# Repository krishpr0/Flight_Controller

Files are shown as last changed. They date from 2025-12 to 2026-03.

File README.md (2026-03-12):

<h1>Flight Controller</h1>

<h5>Flight Controllers developed for Aerial Vehicles</h5>

## Components 
- **STM32F722RET6 MCU**
- **ICM-45686 IMU**
- **BMP580 BARO**
- **QMC5883P MAG**
- **MAX-M10S GPS**
- **3.3V/5V Buck Converters**
- **Micro SD Card Holder**
- **4S LiPO/LiIon**
- **4 Servo/ESCs Pins**

## PCB & Schmeatic Design 
<br>

### Schematic
Screenshot from 2026-02-10 11-39-34

<br>

### PCB


<br>

### 3D Look of the PCB
Screenshot from 2026-02-10 11-39-44

### Operation of the Product
- **Firmware** The firmware used for my current setup is the PX4, Which is know for its autonomus reliablity and efficiency.
- You can use BetaFlight, Inav, CleanFlight, Etc... and even a custom firmware!!

- This Flight Controller was made to be able to communicate with Mission Planner, PX4, etc.
- This is one of my finest creation. All of the Pervious versions were either in a Matrix board, or breadboard.

#### Reasons for making it,
- **Reason**, Firstly the reasons I started into Flight Controllers were because of Drones, I always wanted to know how it worked, how it operated, how it functions, and after looking at articles after articles, I got to know Flight Controller was the most important part for a drone to function. So i started looking at Flight Controllers, Many ppl bought pre-made Flight Controllers such as SpeedyBee, Pixhawk, etc. But those lacked features, altho the features they have are the best of the best, their circuits, But i wanted to have as much features as possible, and as well as work my way up the Flight Controllers, This Flight Controllers will be my first ever PCB made with this much functionality.

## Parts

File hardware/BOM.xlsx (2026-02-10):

No. | Quantity | Comment | Designator | Footprint | Value | Manufacturer Part | Manufacturer | Supplier Part | Supplier
1 | 4 | Test-Point | +5V,GND,U3_RX,U3_TX | Test-Point-0.5mm
2 | 2 | TS-1088-AR02016 | BOOT1,RESET1 | SW-SMD_L3.9-W3.0-P4.45 |  | TS-1088-AR02016 | XUNPU(讯普) | C720477 | LCSC
3 | 5 | Device_C | C7,C8,C9,C12,C31 | C0603 | 10uF
4 | 5 | Device_C | C10,C11,C13,C17,C18 | C0603 | 22uF
5 | 13 | Device_C | C14,C15,C19,C20,C21,C22,C23,C24,C25,C26,C27,C37,C38 | C0603 | 100nF
6 | 2 | Device_C | C16,C32 | C0603 | 2.2uF
7 | 3 | Device_C | C28,C29,C30 | C0603 | 1uF
8 | 2 | Device_C | C33,C34 | C0603 | 20pF
9 | 2 | Device_C | C35,C36 | C0603 | 6.8pF
10 | 1 | Device_C | C40 | C0603 | 4.7uF
11 | 1 | Device_C | C41 | C0603 | 0.1uF
12 | 1 | TF-01A | Card1 | TF-SMD_TF-01A |  | TF-01A | 韩国韩荣 | C91145 | LCSC
13 | 1 | HX PH254-01-04-Z-L11.5 straight pin header | H1 | HDR-TH_4P-HX-PH254-01-04-Z-L11.5 |  | HX PH254-01-04-Z-L11.5 straight pin header | hanxia(韩下) | C52016392 | LCSC
14 | 2 | 1.5uH | L1,L6 | IND-SMD_L4.0-W4.0-A | 1.5uH | XFL4020-152MEC | Coilcraft(线艺) | C3033018 | LCSC
15 | 1 | FCM1608KF-601T03 | L4 | L0603 |  | FCM1608KF-601T03 | TAI-TECH(台庆) | C141723 | LCSC
16 | 1 | 5.6uH | L7 | IND-SMD_L3.0-W3.0 | 5.6uH | YHNR3015-5R6M | YJYCOIN(益嘉源) | C18236327 | LCSC
17 | 1 | LED_0402-R | LED1 | LED0402-RD_YELLOW
18 | 4 | HX PH254-01-03-Z-L11.5 pcb pin header | M1,M2,M3,M4 | HDR-TH_3P-P2.54-V-M-1 |  | HX PH254-01-03-Z-L11.5 pcb pin header | hanxia(韩下) | C52016391 | LCSC
19 | 1 | PDTC114EU,115 | Q1 | SOT-323-3_L2.0-W1.3-P1.30-LS2.1-BR |  | PDTC114EU,115 | Nexperia(安世) | C135830 | LCSC
20 | 2 | Device_R | R1,R2 | C0201 | 5.1K
21 | 9 | Device_R | R12,R13,R16,R17,R18,R19,R20,R21,R22 | C0201 | 10K
22 | 1 | Device_R | R14 | C0201 | 100K
23 | 1 | Device_R | R15 | C0201 | 22.1K
24 | 1 | Device_R | R23 | C0201 | 820
25 | 1 | Device_R | R24 | C0201 | 10
26 | 2 | Device_R | R25,R26 | C0201 | 4.7k
27 | 1 | 6GHz | RF1 | RF-SMD_U.FL-R-SMT-1-80 | 6GHz | U.FL-R-SMT-1(01) | HRS(广濑) | C598199 | LCSC
28 | 1 | ICM-45686 | U2 | LGA-14_L3.0-W2.5-P0.50-TL |  | ICM-45686 | TDK InvenSense(应美盛) | C22459454 | LCSC
29 | 1 | STM32F722RET6 | U3 | LQFP-64_L10.0-W10.0-P0.50-LS12.0-BL |  | STM32F722RET6 | ST(意法半导体) | C118207 | LCSC
30 | 1 | TPS63070RNMR | U5 | VQFN-HR-15_L3.0-W2.5-P0.50-BL_TPS63070RNMR |  | TPS63070RNMR | TI(德州仪器) | C109322 | LCSC
31 | 1 | LMR51430XDDCR | U6 | SOT-23-6_L2.9-W1.6-P0.95-LS2.8-BL |  | LMR51430XDDCR | TI(德州仪器) | C5185863 | LCSC
32 | 1 | MAX-M10S-00B | U7 | SMD-18_L10.1-W9.7-P1.10-TL_SKG09F |  | MAX-M10S-00B | U-BLOX | C4153167 | LCSC
33 | 1 | QMC5883P | U8 | LGA-16_L3.0-W3.0-P0.50-BL_SQ |  | QMC5883P | QST(上海矽睿) | C2847467 | LCSC
34 | 1 | BMP580 | U9 | LGA-10_L2.0-W2.0-P0.50-TL_BMP580 |  | BMP580 | Bosch(博世) | C22391138 | LCSC
35 | 1 | TYPE-C 16PIN 2MD(073) | USB1 | USB-C-SMD_TYPE-C-6PIN-2MD-073 |  | TYPE-C 16PIN 2MD(073) | SHOU HAN(首韩) | C2765186 | LCSC
36 | 1 | 25MHz | X1 | CRYSTAL-SMD_4P-L3.2-W2.5-BL | 25MHz | X322525MOB4SI | YXC(扬兴晶振) | C9006 | LCSC
37 | 1 | 32.768kHz | X2 | OSC-SMD_2P-L3.2-W1.5 | 32.768kHz | ABS07-32.768KHZ-T | ABRACON | C130253 | LCSC

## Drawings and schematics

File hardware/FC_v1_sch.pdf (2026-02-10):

# Pressure Sensor

# IMU

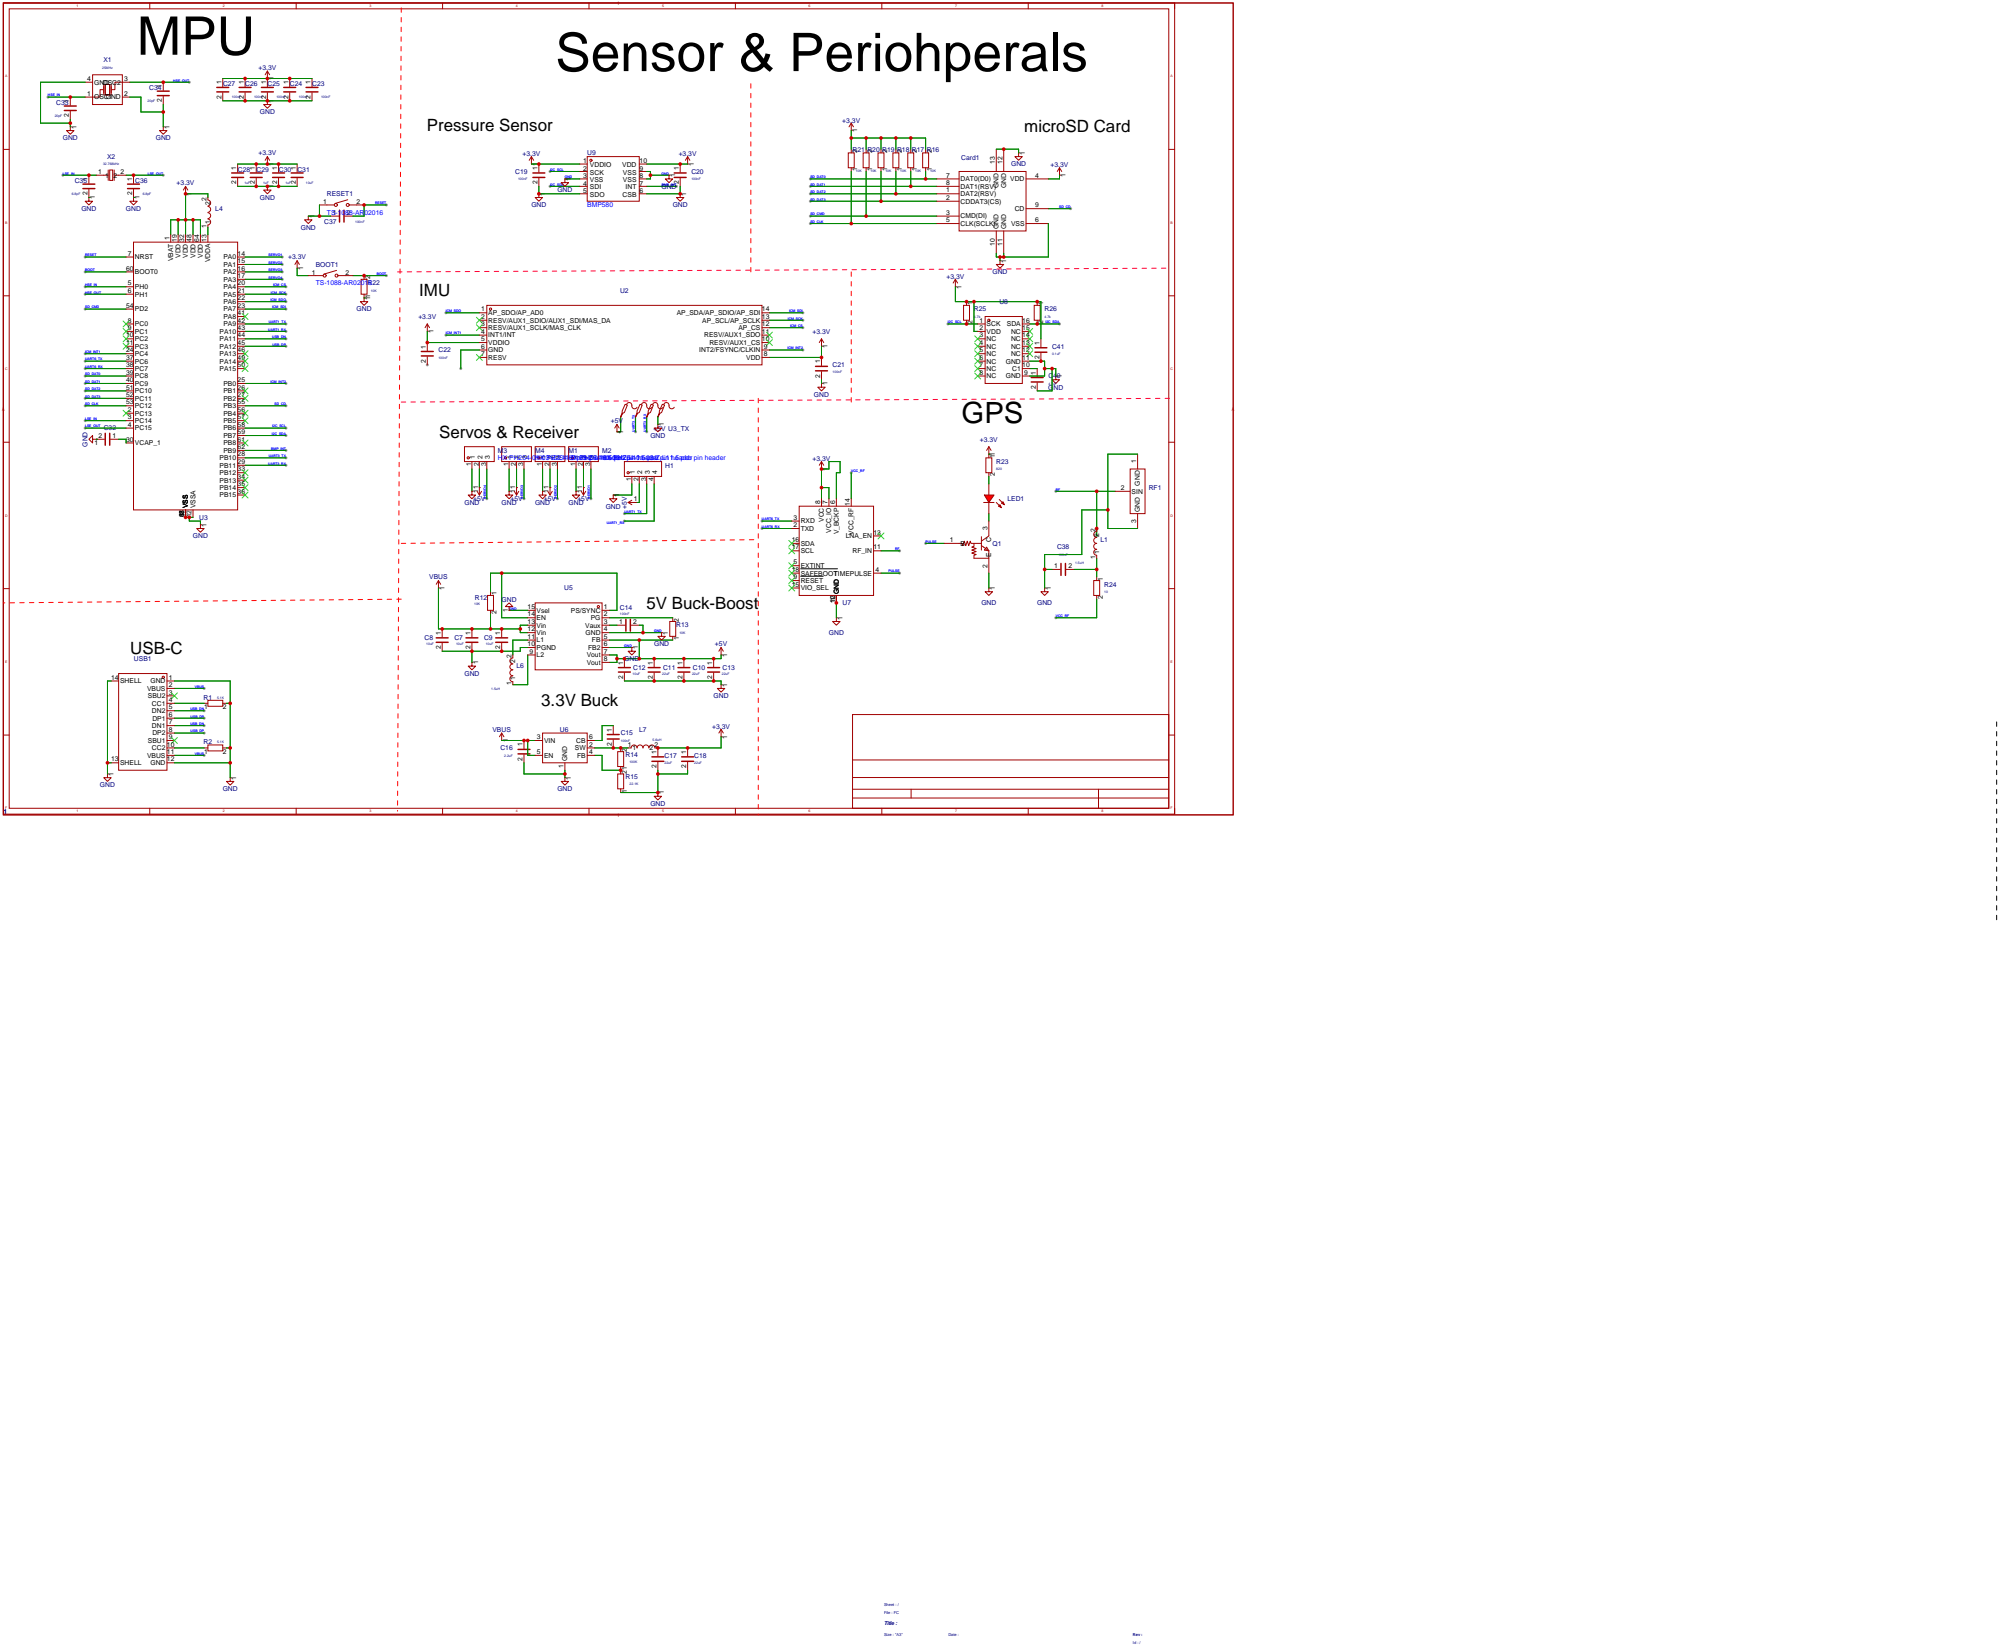
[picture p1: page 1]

HX PH254-01-03-Z-L11.5 pcb pin header

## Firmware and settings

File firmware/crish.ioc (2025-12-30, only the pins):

Mcu.UserName=STM32F722RETx
PA0-WKUP.Signal=S_TIM2_CH1_ETR
PA1.Signal=S_TIM2_CH2
PA10.Signal=USART1_RX
PA11.Signal=USB_OTG_FS_DM
PA12.Signal=USB_OTG_FS_DP
PA2.Signal=S_TIM2_CH3
PA3.Signal=S_TIM2_CH4
PA4.Signal=SPI1_NSS
PA5.Signal=SPI1_SCK
PA6.Signal=SPI1_MISO
PA7.Signal=SPI1_MOSI
PA9.Signal=USART1_TX
PB0.Signal=GPXTI0
PB10.Signal=USART3_TX
PB11.Signal=USART3_RX
PB3.Signal=GPIO_Input
PB5.Signal=GPXTI5
PB6.Signal=I2C1_SCL
PB7.Signal=I2C1_SDA
PB8.Signal=GPIO_Output
PB9.Signal=GPXTI9
PC10.Signal=SDMMC1_D2
PC11.Signal=SDMMC1_D3
PC12.Signal=SDMMC1_CK
PC14-OSC32_IN.Signal=RCC_OSC32_IN
PC15-OSC32_OUT.Signal=RCC_OSC32_OUT
PC4.Signal=GPXTI4
PC6.Signal=USART6_TX
PC7.Signal=USART6_RX
PC8.Signal=SDMMC1_D0
PC9.Signal=SDMMC1_D1
PD2.Signal=SDMMC1_CMD
PH0-OSC_IN.Signal=RCC_OSC_IN
PH1-OSC_OUT.Signal=RCC_OSC_OUT

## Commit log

2025-12-27 Flight Controller
    [FC.kicad_pcb, FC.kicad_sch]
2025-12-27 Added a hole in the PCB for holding it to the FC of mine.
    [FC.kicad_pcb]
2025-12-27 Added the BOM
    [bom.csv]
2025-12-27 fixed a few errors in the PCB
    [FC.kicad_pcb]
2025-12-30 trying to add the GPS with the more servo functions and emptying of UARTs ports as much as possible
    [FC.kicad_pcb, FC.kicad_sch]
2026-01-11 Srinked the size of the FC with adding the GPS in progress and also trying to make the FC small as opssible.
    [FC.kicad_pcb, FC.kicad_sch]
